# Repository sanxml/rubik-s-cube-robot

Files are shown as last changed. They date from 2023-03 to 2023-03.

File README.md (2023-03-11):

# 双臂魔方机器人

- [双臂魔方机器人](#双臂魔方机器人)
  - [设备总体设计方案](#设备总体设计方案)
    - [整体流程](#整体流程)
  - [硬件设计](#硬件设计)
    - [机械结构](#机械结构)
  - [软件设计](#软件设计)
    - [运动控制算法设计](#运动控制算法设计)
    - [图像处理设计](#图像处理设计)
    - [魔方算法设计](#魔方算法设计)
    - [GUI界面设计](#gui界面设计)

## 设备总体设计方案

### 整体流程

整体流程为:本作品以Arduino UNO单片机为控制核心，树莓派为图形处理核心。用DM542C数字驱动器驱动42步进电机实现机器手臂的“手腕”转动，单片机发送PWM信号能够控制20kg大扭矩数字伺服电机，以实现机器人手臂的“手指”收合。我们使用树莓派外接7寸显示屏和自主设计的GUI界面作为显示和操作终端，通过摄像头识别魔方颜色，通过树莓派对结果进行处理，用串口发送机器手臂的可执行信号给Arduino UNO，再通过Arduino控制机械手臂，完成魔方的复原。

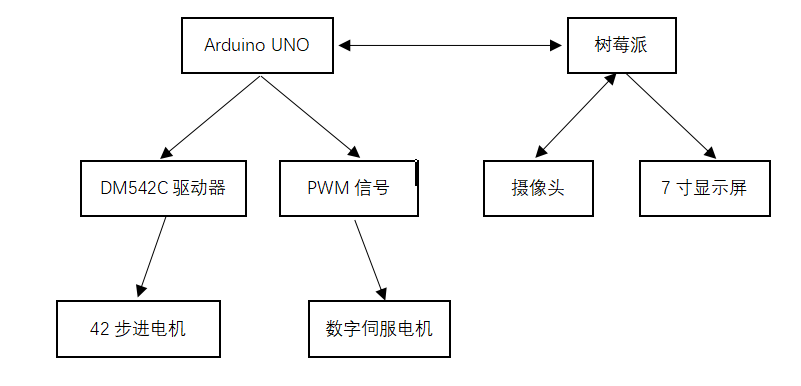
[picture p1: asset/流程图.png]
流程图


## 硬件设计

### 机械结构

本作品的总体机械结构呈现直立双臂魔方机器人，包括机械手臂和摄像头支架等。魔方采用斜放放置，摄像头俯视整个魔方，确保加快魔方的颜色识别。机械臂转动驱动使用步进电机，机械爪使用平行爪，确保平稳的抓取魔方，总体三维建模使用solidworks软件，三维模型文件在 model 目录下。

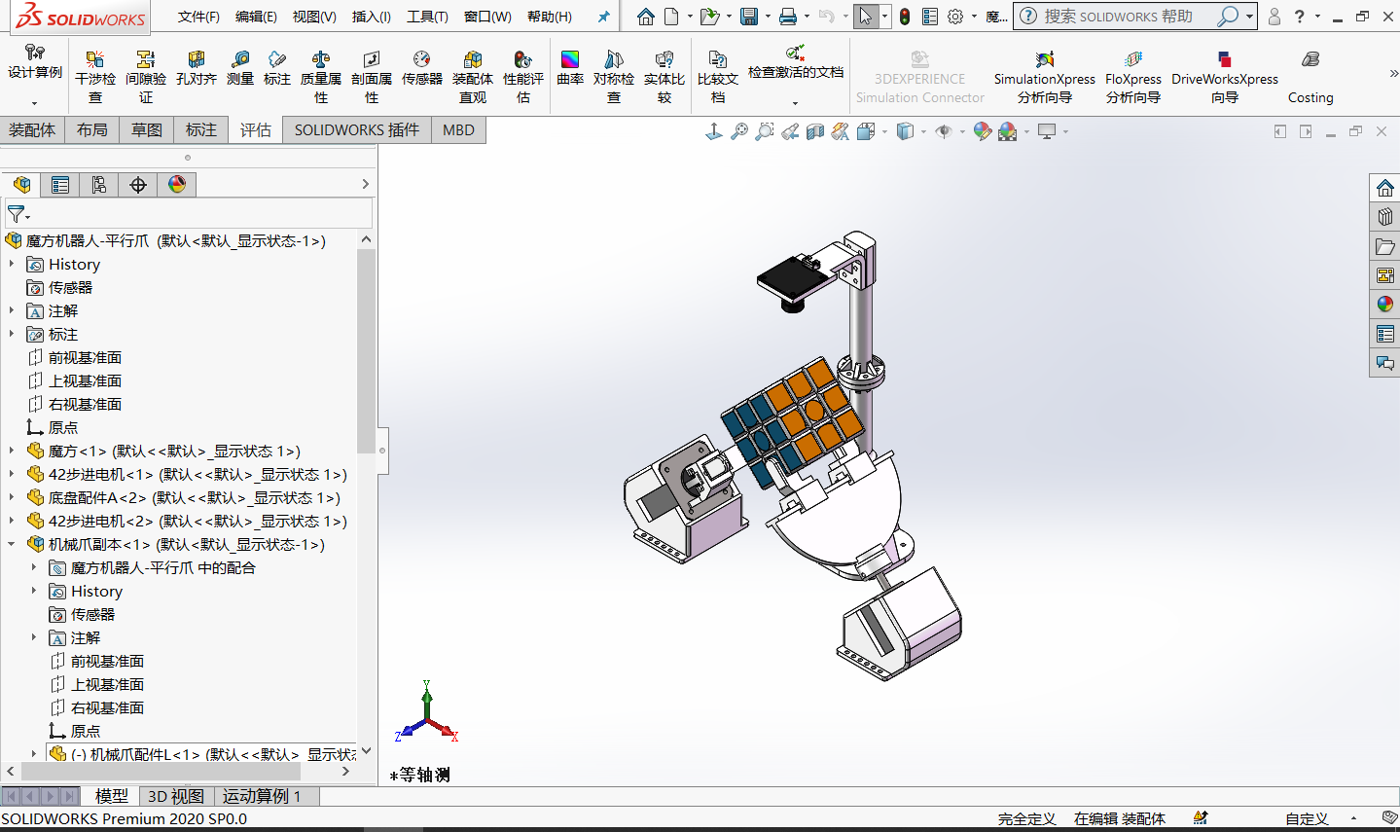
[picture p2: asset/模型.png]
模型


## 软件设计

### 运动控制算法设计

运动控制采用Arduino UNO单片机实现，使用串口连接树莓派，等待树莓派对魔方状态进行程序分析，得到魔方还原序列发送给Arduino UNO单片机。Arduino UNO单片机再将数据进行处理，控制电机实现魔方的复原。

步进电机属于开环系统，容易出现丢步和抖动等现象，硬件上对输入电流的控制和驱动器细分选择外，软件上还可以通过缓慢启停步进电机实现，通过改变给步进电机驱动器的脉冲快慢可以实现，具体实现代码如下

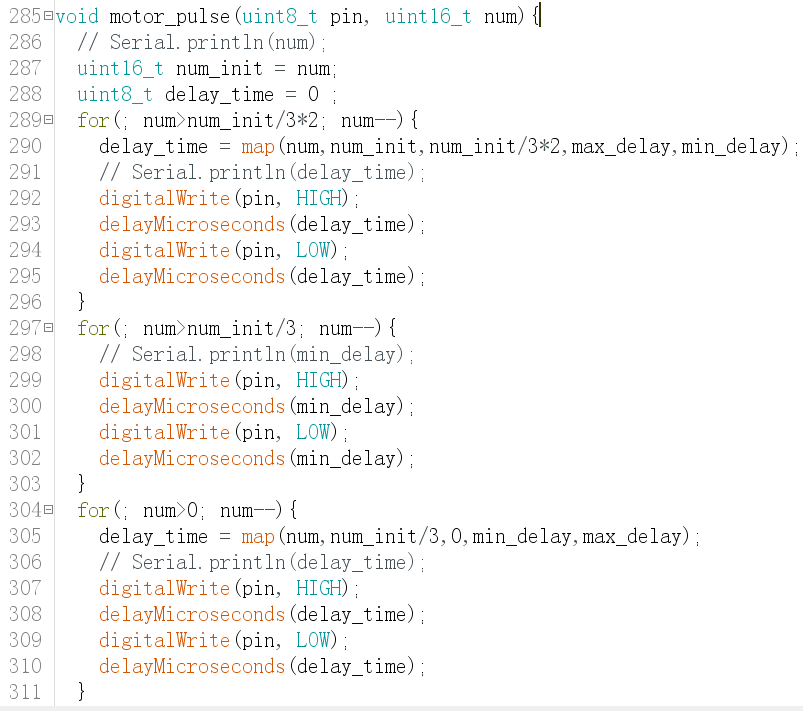
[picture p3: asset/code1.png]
code1


除此之外，步进电机如果一直往一个方向转动，会使舵机的信号线和机器手臂缠绕。为了避免这种情况发生，我们为每一个机器手臂设置一个标志变量，每次执行180度转动时，反转标志位，使下一次180度转动为相反反向。具体实现代码如下。

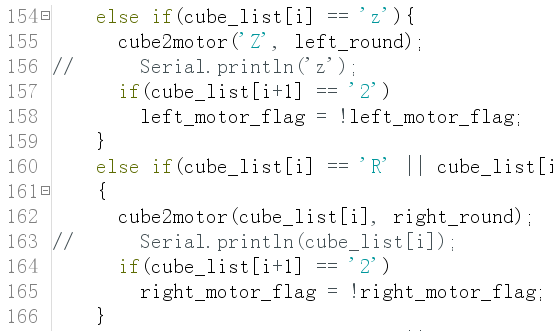
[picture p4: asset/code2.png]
code2


具体控制代码见[代码](code/arduino/cube12_01.ino)

### 图像处理设计

本作品中图像处理的整体思路：使用树莓派控制摄像头进行拍摄，把魔方的初始状态拍成图片，处理图片并将魔方每一面的颜色和魔方的位置存储到文本中；再对存储的文本内容进行分析，采用二阶段算法得到还原魔方的解法，再将六面转动解法通过优化生成二指还原解法，发送给Arduino UNO单片机对魔方进行复原。

图像处理程序均用python编程语言和opencv图像处理库实现。树莓派发送转动指令给Arduino单片机，转动三次，一次拍摄两面，将魔方初始状态通过照片存储起来。先对图片进行简单的高斯模糊去噪处理，再分割成单面图像。因为魔方位置是固定的，这里只需要对图片的特定位置进行分割，再通过文本矫正将不规则的梯形转成矩形，分割前后的图片和分割部分的关键程序代码分别如下图。

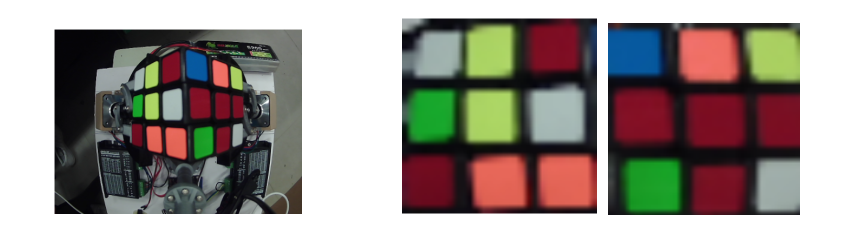
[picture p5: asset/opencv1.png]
opencv1


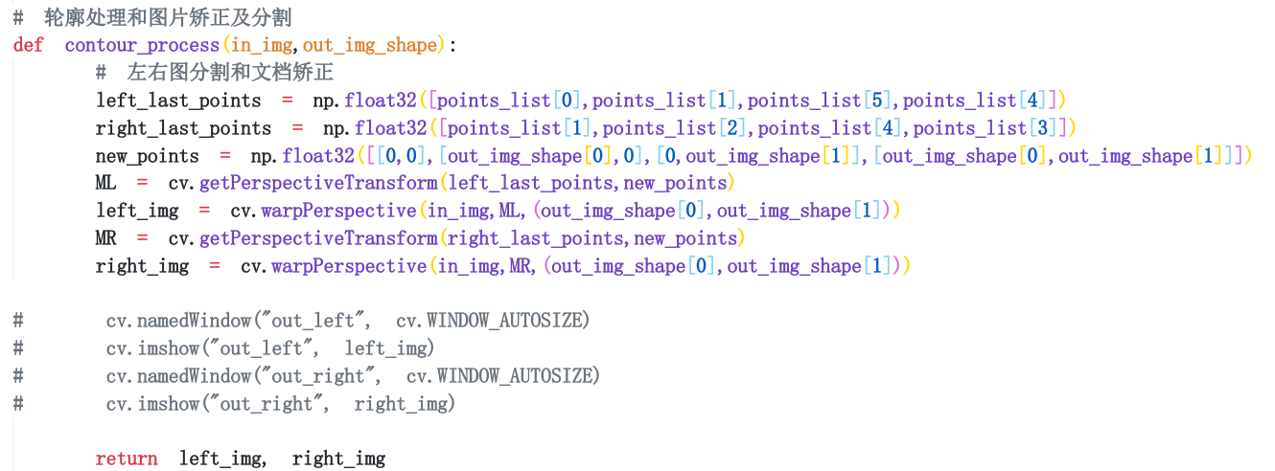
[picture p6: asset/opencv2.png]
opencv2


颜色识别采用将图片色彩空间从传统的RGB转换成HSV和LAB，HSV即色相(Hue)、饱和度(Saturation)、明度(Value)，又称HSB(B即Brightness)。H色相是色彩的基本属性，HSV色彩空间对颜色判断灵敏，且颜色识别时不易受明亮度的影响；Lab颜色被设计来接近人类视觉。它致力于感知均匀性，它的L分量密切匹配人类亮度感知。因此可以被用来通过修改a和b分量的输出色阶来做精确的颜色平衡，或使用L分量来调整亮度对比。

两种色彩空间都可以有效的减少因为环境光增加识别魔方的难度，这里采用双色彩空间进行矫正，RGB和LAB色彩空间、HSV色彩空间的对比图如下。

opencv3

在图片分割矫正和色彩空间转换后，就要将魔方每一个面的九个色块的LAB和HSV色彩空间的值都存储起来，以便后续进行颜色识别分类，相应代码如下图。

具体图像处理代码见[代码](code/raspberry-pi/cube.py)

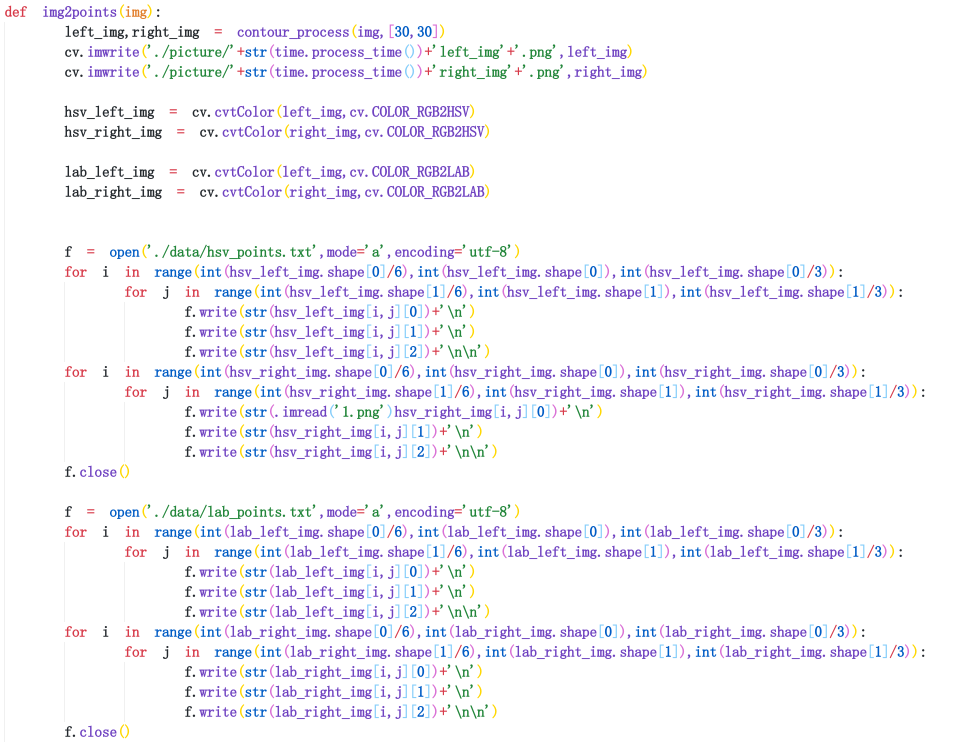
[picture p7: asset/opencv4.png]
opencv4


最后的就是程序最为重要的颜色识别分类，我采用的是多次循环HSV和LAB双色彩空间矫正的K-means聚类算法，对不同的光照的环境都能很好的识别。HSV和LAB色彩空间识别生成的三维图分别如下图。

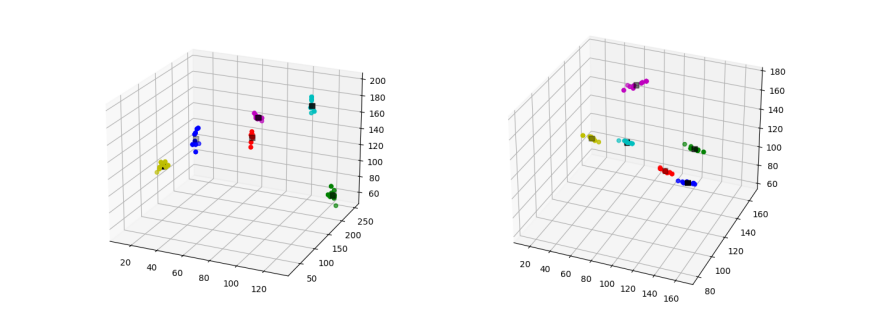
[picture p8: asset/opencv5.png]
opencv5


具体聚类代码见[代码](code/raspberry-pi/kmeans.py)

### 魔方算法设计

解魔方比赛中，主流的魔方解法，无论是从入门的层先，到进阶的CFOP、桥式，都是从部分到整体的思路，逐块还原魔方。这种方法之所以能在速拧比赛中广泛应用，依赖于人眼与人脑快速反应的结合，但这种解法并不适合与计算机。

机器的优势在于广度搜索与深度搜索能力，解魔方算法采用二阶段算法，也称为Kociemba算法，通过降低魔方的混乱程度，达到复原的效果。这种魔方解法的步数可以控制在21步以内，通过转换为二指解法也不过需要四十到七十步左右，二阶段算法还原魔方的示意图如图

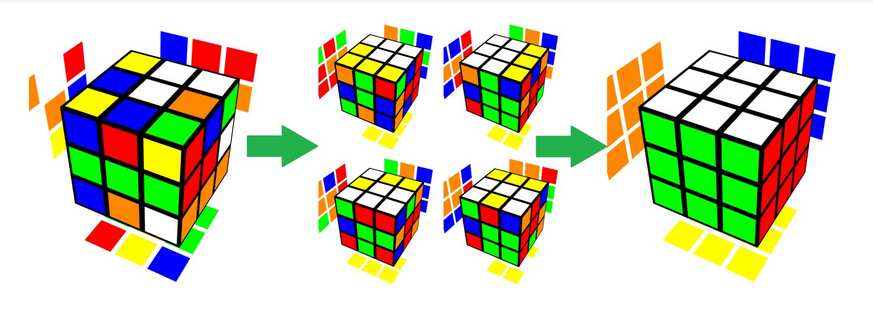
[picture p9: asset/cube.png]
cube


仅仅通过前面采集到的魔方每一面的颜色序列，还不能直接使用二阶段算法，需要提前设置每一面的相对位置，例如设定为白上绿前，但这是不现实的，不能得知乱魔方放置的初始位置，通过归类，可以得到一共由8种不同的相对位置。判断识别面中心的顺序，可以旋转面的颜色序列，达到实现白上绿前的相对位置。

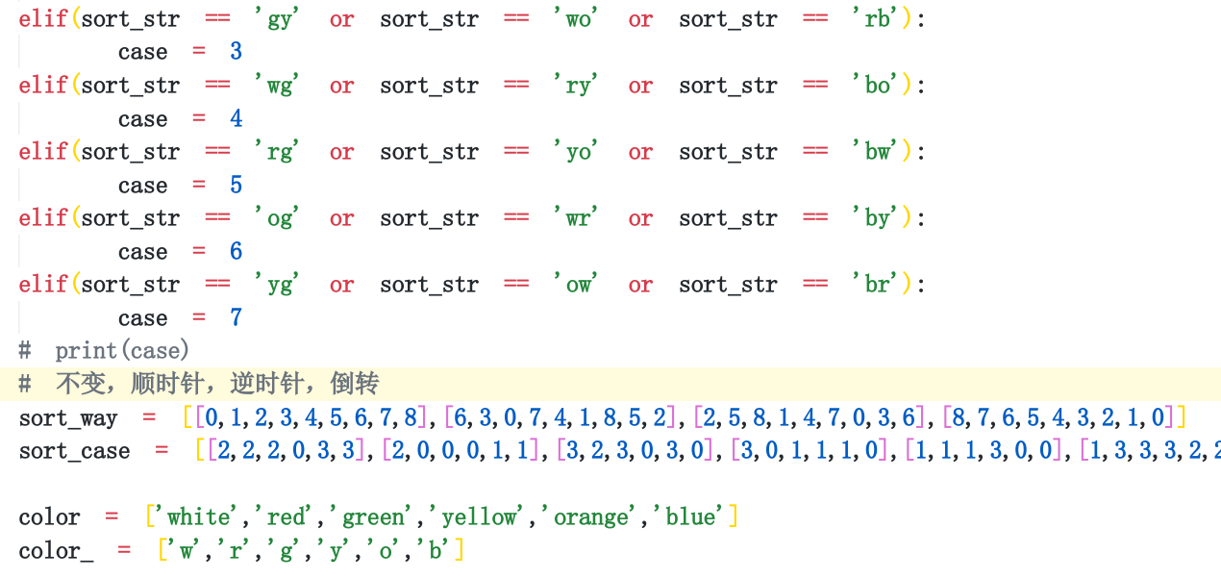
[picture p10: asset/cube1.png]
cube1


在调整旋转对应面的模仿序列后，还需要添加实际魔方序列和设定魔方序列 ”白上绿前”的相互关系，即将任意序列转到设定序列的转动步骤，则读取识别面的顺序文件，得到识别的前两面，即得到实际坐标。

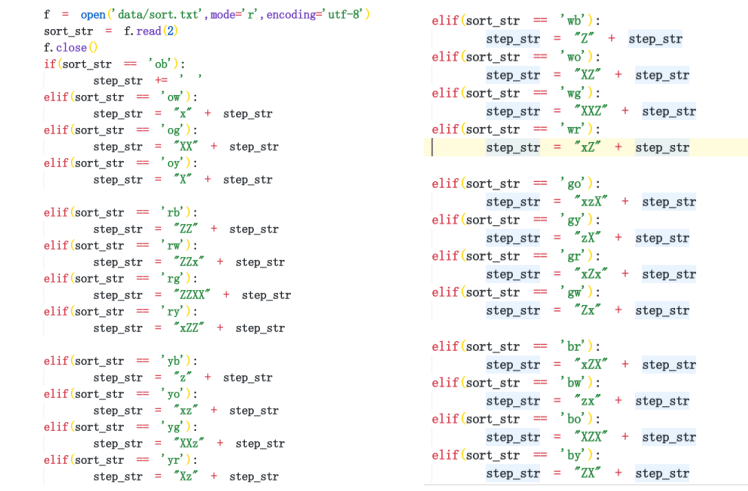
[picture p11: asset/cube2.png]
cube2


就可以使用二阶段算法了。使用二阶段算法，针对任意一个乱魔方都可以得到一串只有不到21步的还原公式。本作品设计的是一款双臂的魔方机器人，无法同时对六个面进行转动；通过对另外只能间接控制的面转换成两个可以同时控制的面的公式，即可实现通过双臂机器人还原魔方。转换后，得到的还原公式还比较繁琐，需要进一步优化，例如顺时针旋转一面三圈相当于逆时针旋转一圈。转换过程如图所示。

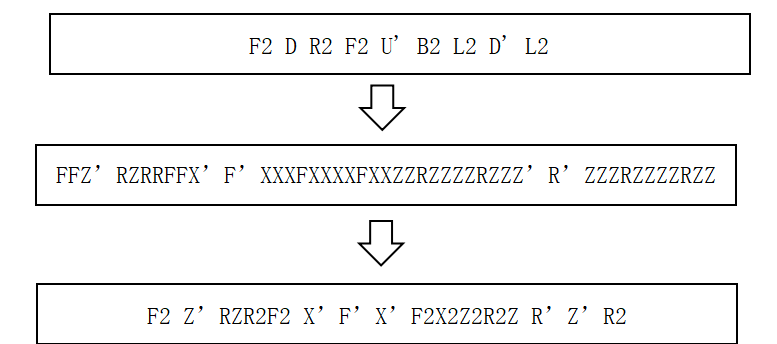
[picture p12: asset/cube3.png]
cube3


具体魔方算法代码见[代码](code/raspberry-pi/solution.py)

### GUI界面设计

本作品使用一块树莓派外接7寸显示屏，可触控。决定设计一个GUI交互界面，方便显示魔方的实况和解法等信息，以及可以实现一键解魔方的功能。

GUI界面主要由四部分组成，左上部分为摄像头的实时图像，可以方便显示魔方的实况；右上部分为识别到的魔方序列图解，可以全面的显示识别结果以及魔方整体的初始状态；左下部分为文本框，显示魔方的解法等信息；右下角有两个用户按键，一个可以发送转动信号，得到魔方的初始状态，另一个则是一键运行解魔方程序，具体界面如图5-3-1所示。

具体GUI界面代码见[代码](code/raspberry-pi/gui.py)

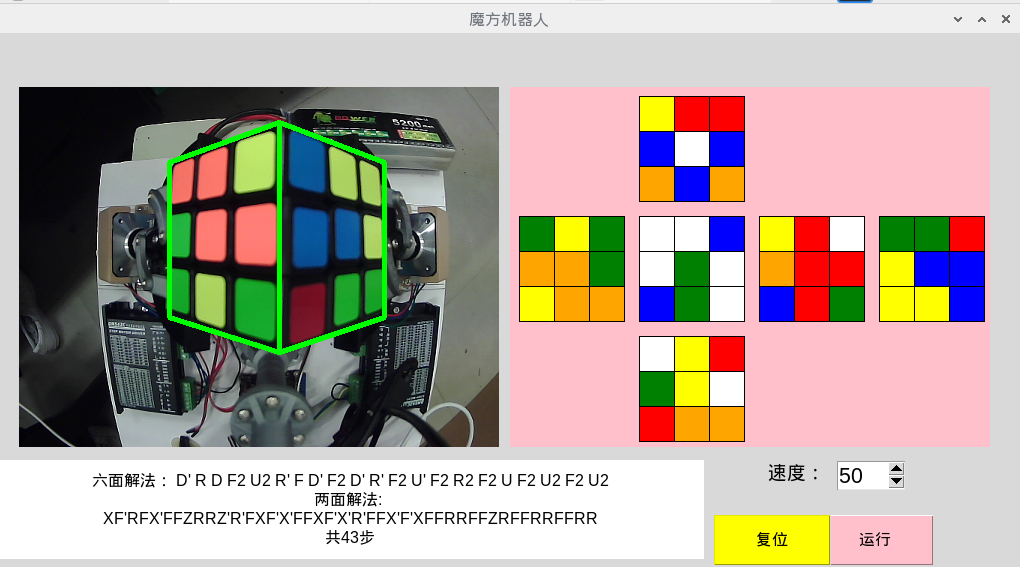
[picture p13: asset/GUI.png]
GUI


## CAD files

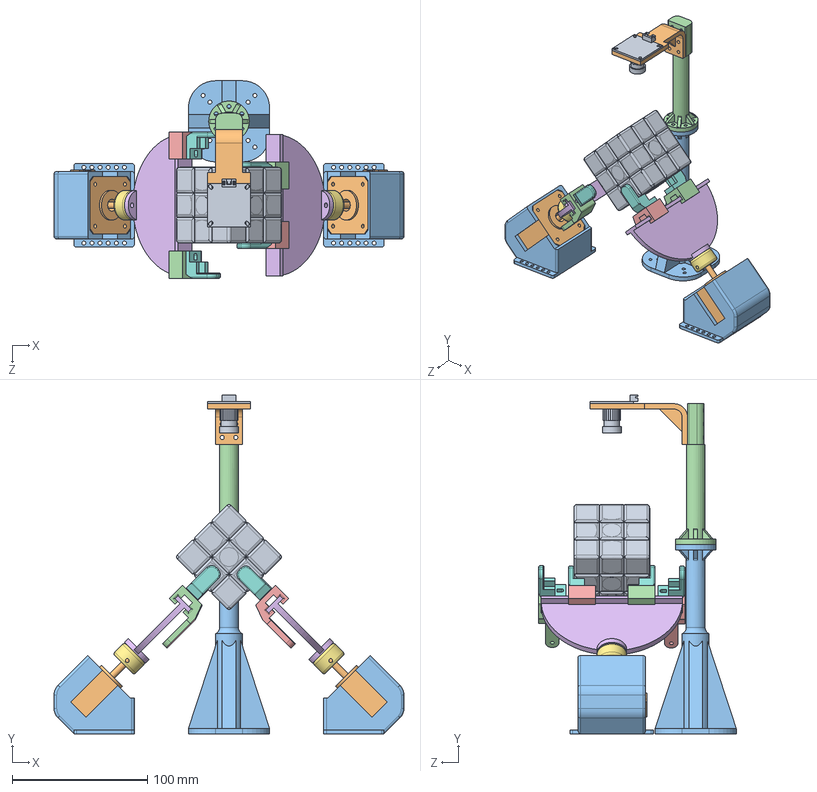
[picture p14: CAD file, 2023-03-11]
model/魔方机器人-平行爪.SLDASM
258.6 x 250.3 x 146.0 mm
魔方
42步进电机 x 2
底盘配件A x 2
机械爪配件L x 2
机械爪配件R x 2
机械爪配件A x 2
机械爪配件B x 2
机械爪配件C x 4
usb摄像头
底盘配件B
底盘配件C
底盘配件D

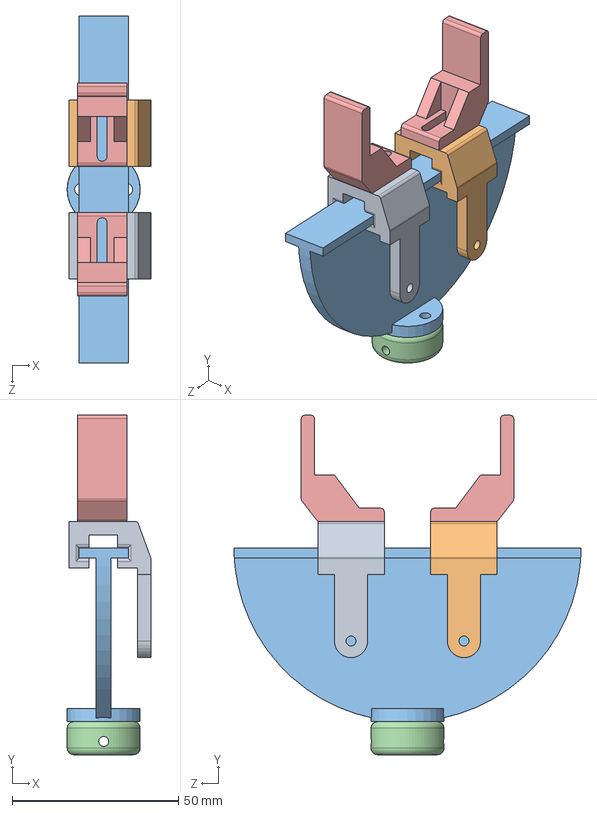
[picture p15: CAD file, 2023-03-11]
model/机械爪副本.SLDASM
25.2 x 102.2 x 104.5 mm
机械爪配件L
机械爪配件R
机械爪配件A
机械爪配件B
机械爪配件C x 2

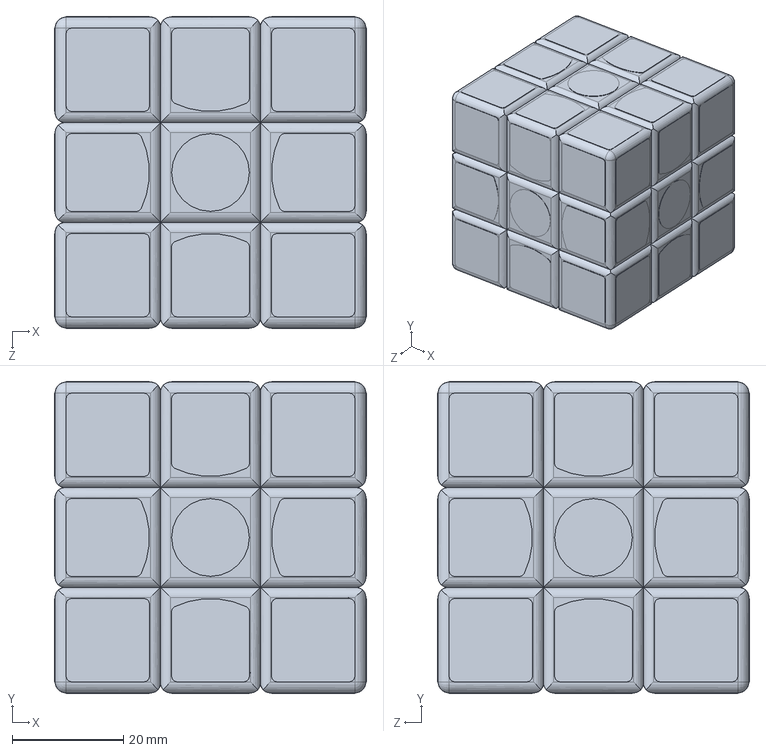
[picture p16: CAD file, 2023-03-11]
model/魔方.SLDPRT
56.2 x 56.2 x 56.2 mm

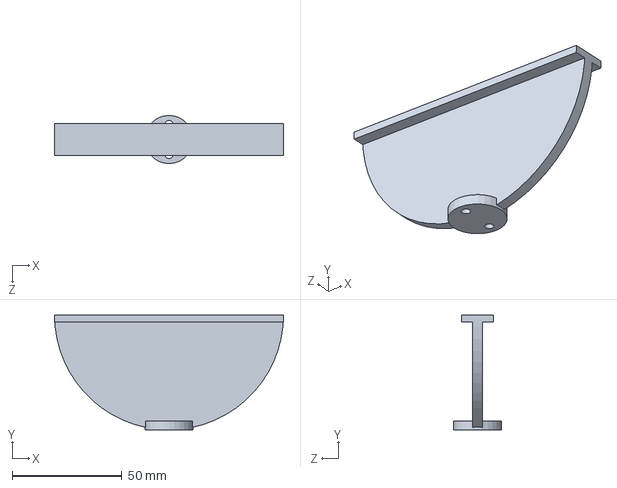
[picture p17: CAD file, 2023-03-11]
model/机械爪配件A.SLDPRT
104.5 x 52.2 x 22.0 mm

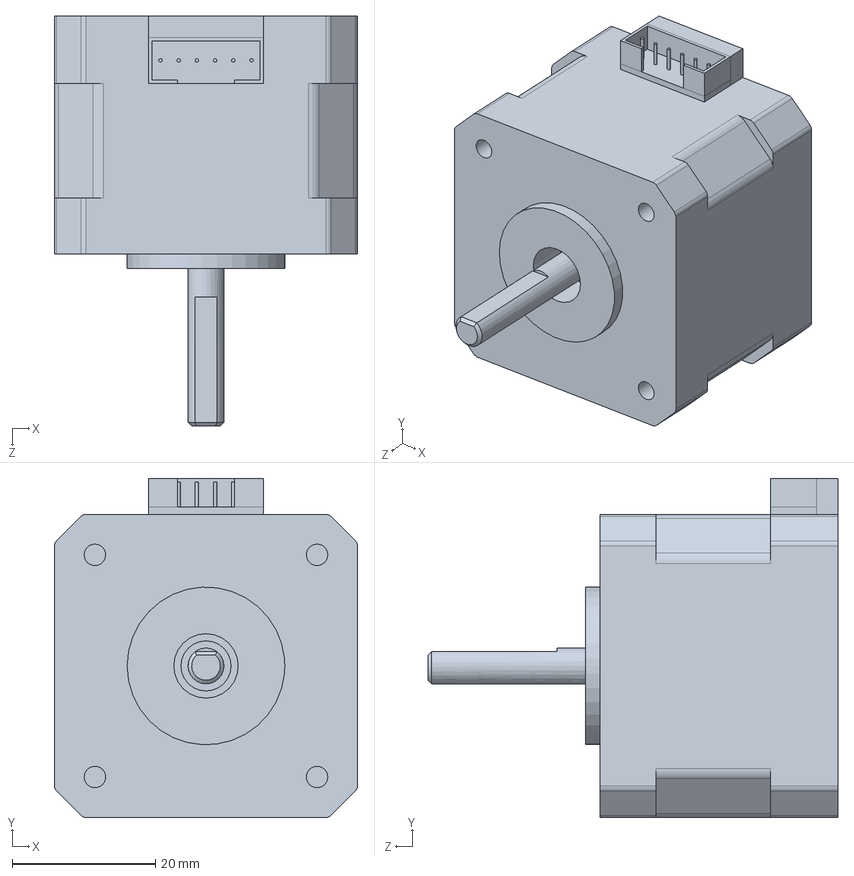
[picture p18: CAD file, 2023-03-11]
model/42步进电机.SLDPRT
42.3 x 47.3 x 57.2 mm

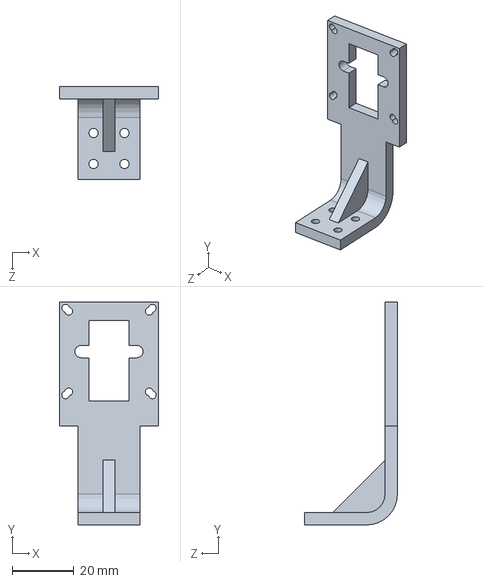
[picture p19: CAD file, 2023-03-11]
model/底盘配件B.SLDPRT
32.0 x 72.0 x 30.0 mm

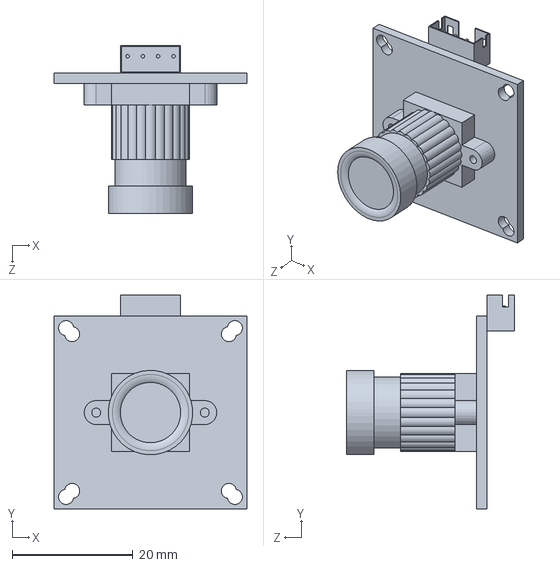
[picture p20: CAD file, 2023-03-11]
model/usb摄像头.SLDPRT
32.0 x 35.5 x 27.9 mm

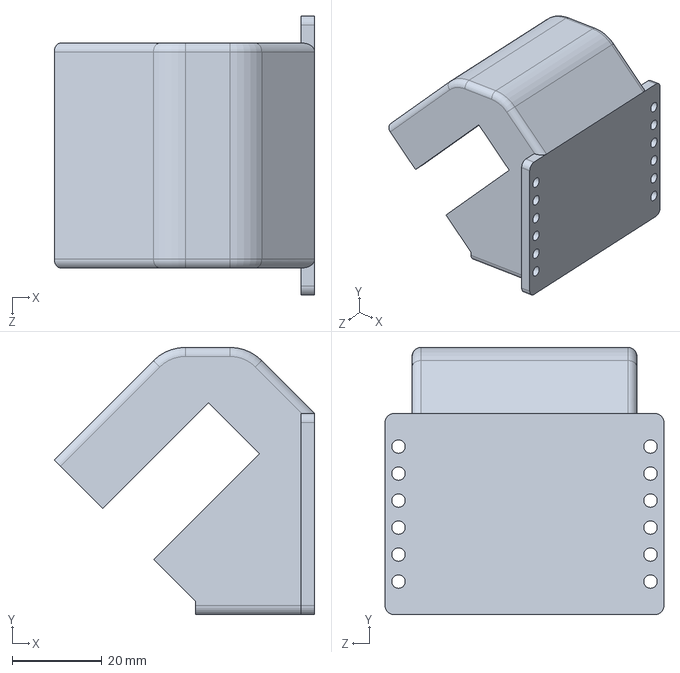
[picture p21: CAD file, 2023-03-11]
model/底盘配件A.SLDPRT
57.9 x 59.4 x 62.0 mm

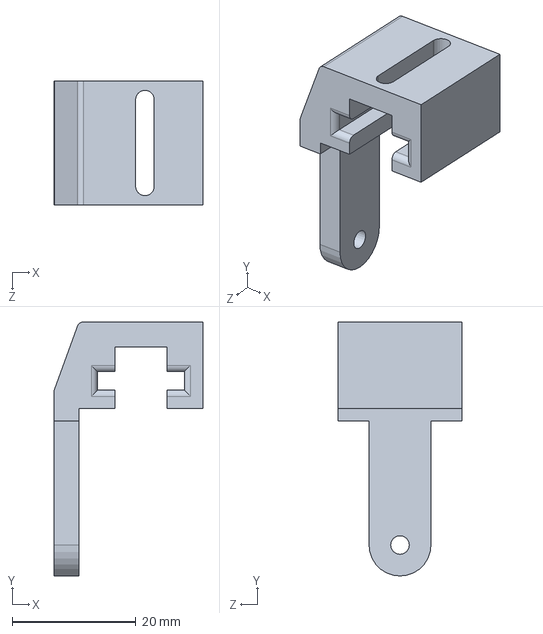
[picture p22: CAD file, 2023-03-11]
model/机械爪配件L.SLDPRT
24.0 x 41.0 x 20.0 mm

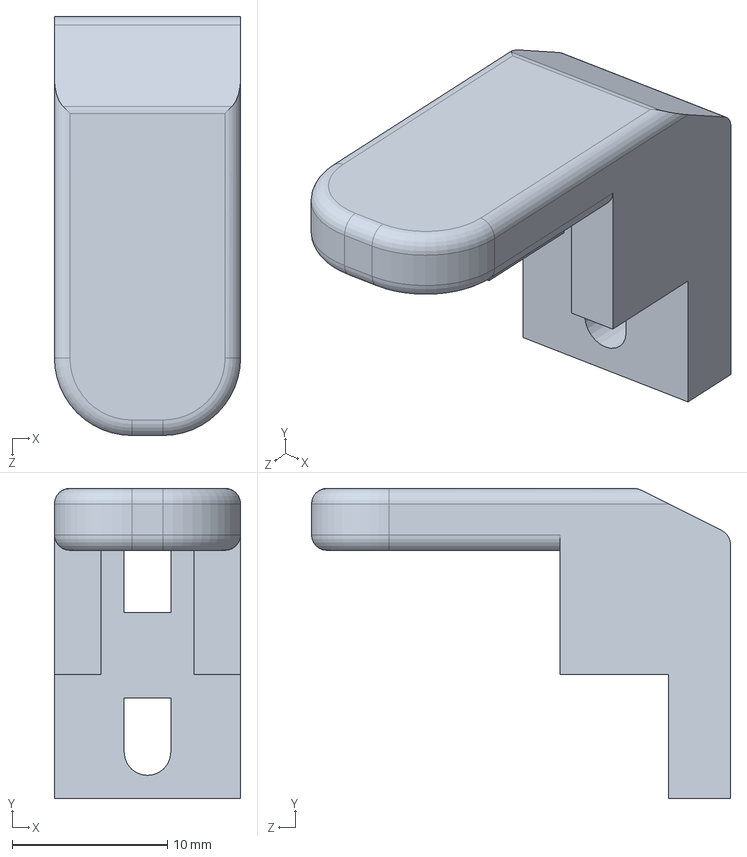
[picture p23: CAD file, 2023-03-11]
model/机械爪配件C.SLDPRT
12.0 x 20.0 x 27.0 mm

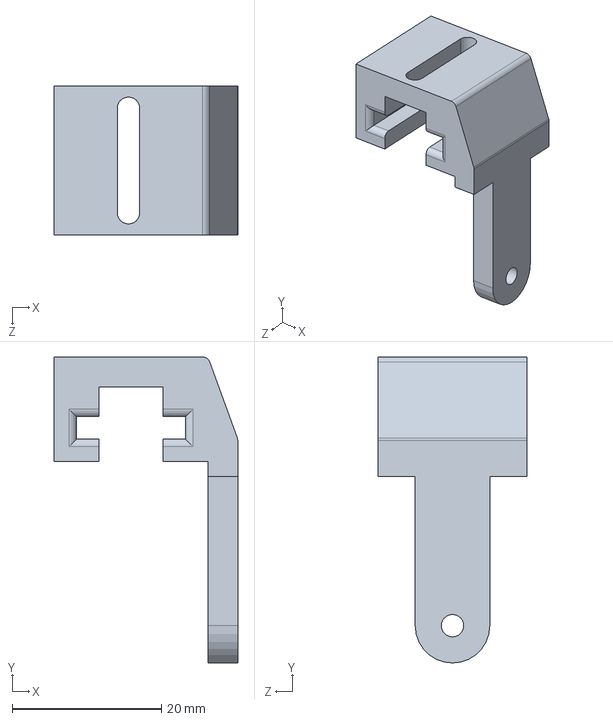
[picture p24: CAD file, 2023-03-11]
model/机械爪配件R.SLDPRT
24.6 x 41.0 x 20.0 mm

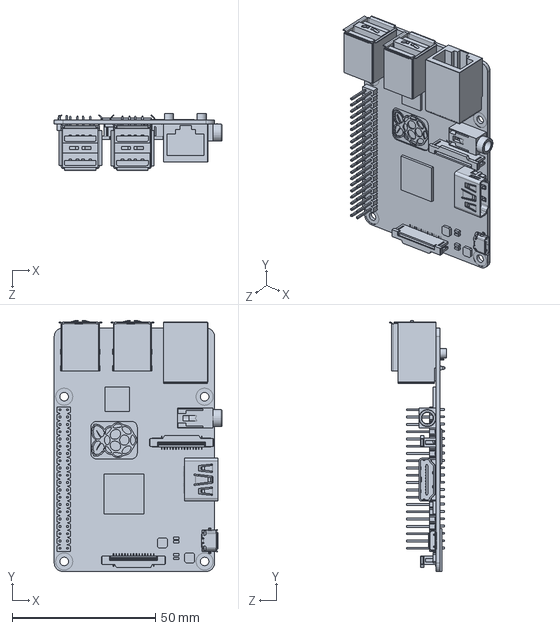
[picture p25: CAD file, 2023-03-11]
model/树莓派3b.SLDPRT
58.5 x 87.6 x 19.8 mm

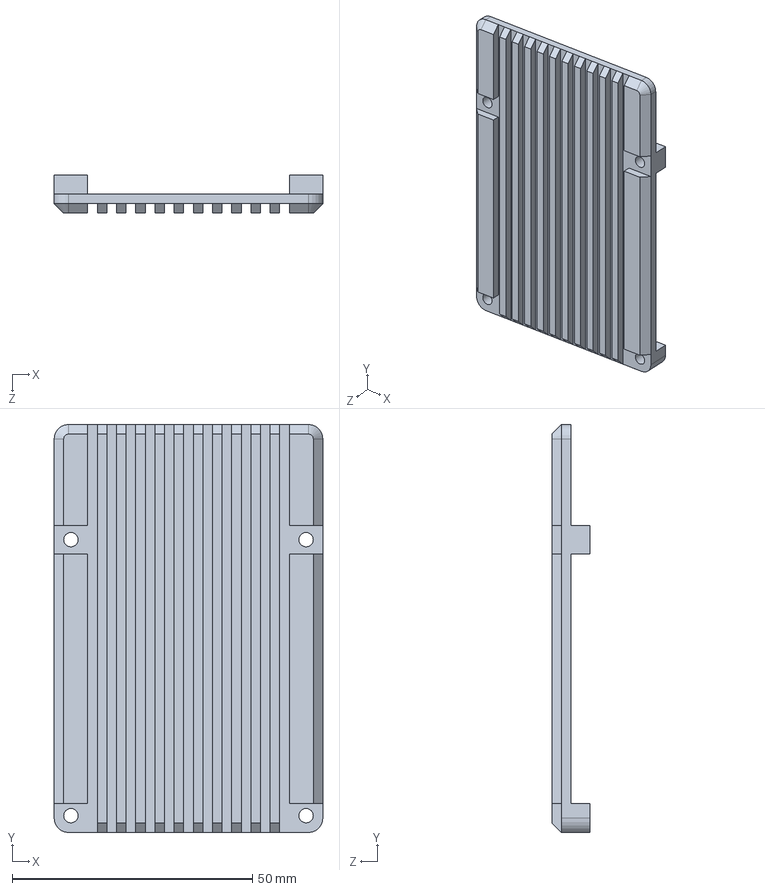
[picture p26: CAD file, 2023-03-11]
model/树莓派底壳.SLDPRT
56.0 x 85.0 x 8.00 mm

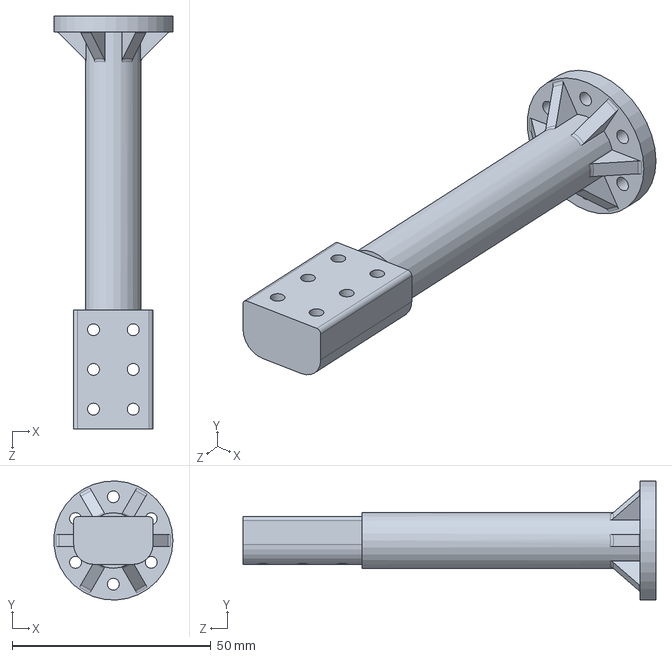
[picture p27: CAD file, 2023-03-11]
model/底盘配件D.SLDPRT
29.9 x 30.0 x 104.0 mm

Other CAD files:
model/机械爪.SLDASM
model/树莓派CSI摄像头.SLDPRT
model/机械爪配件B.SLDPRT
model/底盘配件C.SLDPRT

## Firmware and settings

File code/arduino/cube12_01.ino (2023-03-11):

#include <Servo.h>

#define MOTOR1_CP 3
#define MOTOR1_DIR 4
#define MOTOR1_EN 5
#define MOTOR2_CP 6
#define MOTOR2_DIR 7
#define MOTOR2_EN 8
#define SERVO1 10
#define SERVO2 11

#define MOTOR_PULSE 6400 //转一圈的脉冲

Servo servo_left, servo_right;
uint8_t servo_left_state[4] = {24,38,88,44};// 闭合 紧贴 张开
uint8_t servo_right_state[4] = {24,38,88,44};// 闭合 紧贴 张开  

uint8_t min_delay = 54 , max_delay = 800;

void setup()
{
//  pinMode(LED_BUILTIN, OUTPUT);
  pinMode(MOTOR1_CP, OUTPUT);
  pinMode(MOTOR1_DIR, OUTPUT);
  pinMode(MOTOR1_EN, OUTPUT);
  pinMode(MOTOR2_CP, OUTPUT);

  pinMode(MOTOR2_DIR, OUTPUT);
  pinMode(MOTOR2_EN, OUTPUT);
  digitalWrite(MOTOR1_DIR, HIGH);
  digitalWrite(MOTOR1_EN, LOW);
  digitalWrite(MOTOR2_DIR, HIGH);
  digitalWrite(MOTOR2_EN, LOW);

  Serial.begin(115200); //打开串口

  servo_left.attach(SERVO1,500,2500);
  servo_right.attach(SERVO2,500,2500);

  servo_left.write(servo_left_state[3]);
  servo_right.write(servo_right_state[3]);
  delay(200);

//  servo_left.write(servo_left_state[0]);
//  delay(500);
//  servo_right.write(servo_right_state[2]);
//  delay(3000);
//  servo_left.write(servo_left_state[3]);
//  servo_right.write(servo_right_state[3]);
//  delay(3000);
//  servo_left.write(servo_left_state[2]);
//  servo_right.write(servo_right_state[0]);
//  delay(3000);
}

void loop(){

  String buf = "";
  while (Serial.available() == 0);
  while (Serial.available() > 0){
      buf += char(Serial.read());
      delay(5);
  }
  
  if(buf.length()>=65){
    Serial.flush();
    while (Serial.available() == 0);
    while (Serial.available() > 0){
      buf += char(Serial.read());
      delay(5);
    }
  }
  //Serial.print(buf.length());
  motor_solution(buf);
  Serial.println(buf);
  Serial.flush();

} 

//L2 D2 R' F2 D2 F2 U2 L' B2 D2 L' F' D' L U2 R D F' U L
//rzrzRRzRzFZZrZZxfxFXXrZRzRzrZFFzRZRRFFxfxFFXXZZRRZrzRR
//R' D' L2 U F L' U' B R' U R D' F2 D R2 F2 U' B2 L2 D' L2
//L2 D L2 B2 U F2 R2 D' F2 D R' U' R B' U L F' U' L2 D R

void motor_solution(String cube_list){
  uint8_t i = 0;
  for(; i<cube_list.length(); i++){
    // Serial.print(cube_list[i]);
    if(cube_list[i] == 'S'){
      uint8_t cube_speed = (uint8_t)cube_list[i+1]*10 + (uint8_t)cube_list[i+2] - 16;
      Serial.print("Speed = ");
      Serial.println(cube_speed);
      min_delay = cube_speed;
      cube_list = ' ';
   }
    char temp = cube_list[i];
    if (temp == cube_list[i+1]){
      cube_list[i+1] = '2';
      i++;
    }
  }
  // Serial.println(cube_list);
  uint8_t left_motor_flag = 0, right_motor_flag = 0;
  for(i=0; i<cube_list.length(); i++){
    int8_t left_round, right_round;
    if(cube_list[i] == 'r' || cube_list[i] == 'f' || cube_list[i] == 'x' || cube_list[i] == 'z')
      left_round = right_round = -1;
    else
      left_round = right_round = 1;

    if(cube_list[i+1] == '2'){
      if(left_motor_flag == 0)
        left_round = 2;
      else
        left_round = -2;
      if(right_motor_flag == 0)
        right_round = 2;
      else
        right_round = -2;
    }
    if(cube_list[i] == 'r'){
      cube2motor('R', right_round);
//      Serial.println('r');
      if(cube_list[i+1] == '2')
        right_motor_flag = !right_motor_flag;
    }
    else if(cube_list[i] == 'f'){
      cube2motor('F', left_round);
//      Serial.println('f');
      if(cube_list[i+1] == '2')
        left_motor_flag = !left_motor_flag;
    }
    else if(cube_list[i] == 'x'){
      cube2motor('X', right_round);
//      Serial.println('x');
      if(cube_list[i+1] == '2')
        right_motor_flag = !right_motor_flag;
    }
    else if(cube_list[i] == 'z'){
      cube2motor('Z', left_round);
//      Serial.println('z');
      if(cube_list[i+1] == '2')
        left_motor_flag = !left_motor_flag;
    }
    else if(cube_list[i] == 'R' || cube_list[i] == 'X')
    {
      cube2motor(cube_list[i], right_round);
//      Serial.println(cube_list[i]);
      if(cube_list[i+1] == '2')
        right_motor_flag = !right_motor_flag;
    }
    else if(cube_list[i] == 'F' || cube_list[i] == 'Z')
    {
      cube2motor(cube_list[i], left_round);
//      Serial.println(cube_list[i]);
      if(cube_list[i+1] == '2')
        left_motor_flag = !left_motor_flag;
    }
    else if(cube_list[i] == 'C'){
      cube2motor('C', right_round);
//      Serial.println('C');
    }
    else if(cube_list[i] == 'c'){
      servo_left.write(servo_left_state[3]);
      servo_right.write(servo_right_state[3]);
//      Serial.println('c');
    }
    else if(cube_list[i] == 'l'){
      servo_left.write(servo_left_state[0]);
      servo_right.write(servo_right_state[0]);
//      Serial.println('l');
    }
    if(cube_list[i+1] == '2'){
      i++;
//      Serial.println('2');
    }
  }
}

void cube2motor(char cube_list, int8_t round){
  servo_left.write(servo_left_state[0]);
  servo_right.write(servo_right_state[0]);
  delay(80);
  if(cube_list == 'R'){
    servo_right.write(servo_right_state[1]);
    motor_turning('R', round);
    if(round == 1 || round == -1){
      servo_right.write(servo_right_state[2]);
      delay(100);
      motor_turning('R', -round);
    }
  }
  else if(cube_list == 'F'){
    servo_left.write(servo_left_state[1]);
    motor_turning('L', round);
    if(round == 1 || round == -1){
      servo_left.write(servo_left_state[2]);
      delay(100);
      motor_turning('L', -round);
    }
  }
  else if(cube_list == 'X'){

    if(round == 1 || round == -1){
      servo_right.write(servo_right_state[2]);
      delay(100);
      motor_turning('R', -round);
      servo_right.write(servo_right_state[0]);
      delay(80);
      servo_left.write(servo_left_state[2]);
      delay(100);
      motor_turning('R', round);
    }
    else{
      servo_left.write(servo_left_state[2]);
      delay(100);
      motor_turning('R', round);
      servo_left.write(servo_left_state[3]);
      delay(80);
      servo_right.write(servo_right_state[3]);
      delay(100);
    }

  }
  else if(cube_list == 'Z'){
    if(round == 1 || round == -1){
      servo_left.write(servo_left_state[2]);
      delay(100);
      motor_turning('L', -round);
      servo_left.write(servo_left_state[0]);
      delay(80);
      servo_right.write(servo_right_state[2]);
      delay(100);
      motor_turning('L', round);
    }
    else{
      servo_right.write(servo_right_state[2]);
      delay(100);
      motor_turning('L', round);
      servo_right.write(servo_right_state[3]);
      delay(80);
      servo_left.write(servo_left_state[3]);
      delay(100);
    }
  }
  if(cube_list == 'C'){
      servo_right.write(servo_right_state[3]);
      servo_left.write(servo_left_state[3]);
      delay(200);
      servo_right.write(servo_right_state[0]);
      servo_left.write(servo_left_state[0]);
  }
    
    servo_right.write(servo_right_state[0]);
    servo_left.write(servo_left_state[0]);
    delay(120);
    servo_right.write(servo_right_state[1]);
    servo_left.write(servo_left_state[1]);
    delay(50);
}

void motor_turning(char motor, float right_angle){
  uint8_t cp_pin = 0 , dir_pin = 0;
  if(motor == 'L'){
    cp_pin = MOTOR1_CP;
    dir_pin = MOTOR1_DIR;
  }
  else if(motor == 'R'){
    cp_pin = MOTOR2_CP;
    dir_pin = MOTOR2_DIR;
  }
  if(right_angle >= 0){
    digitalWrite(dir_pin, HIGH);
    motor_pulse(cp_pin, (int)(right_angle*MOTOR_PULSE/4));
    // Serial.println(right_angle*MOTOR_PULSE/4);
  }
  else if(right_angle < 0){
    digitalWrite(dir_pin, LOW);
    motor_pulse(cp_pin, -(int)(right_angle*MOTOR_PULSE/4));
  }
}

void motor_pulse(uint8_t pin, uint16_t num){
  // Serial.println(num);
  uint16_t num_init = num;
  uint8_t delay_time = 0 ;
//  for(; num>num_init/3*2; num--){
//    delay_time = map(num,num_init,num_init/3*2,max_delay,min_delay);
//    // Serial.println(delay_time);
//    digitalWrite(pin, HIGH);
//    delayMicroseconds(delay_time);
//    digitalWrite(pin, LOW);
//    delayMicroseconds(delay_time);
//  }
//  for(; num>num_init/3; num--){
//    // Serial.println(min_delay);
//    digitalWrite(pin, HIGH);
//    delayMicroseconds(min_delay);
//    digitalWrite(pin, LOW);
//    delayMicroseconds(min_delay);
//  }
//  for(; num>0; num--){
//    delay_time = map(num,num_init/3,0,min_delay,max_delay);
//    // Serial.println(delay_time);
//    digitalWrite(pin, HIGH);
//    delayMicroseconds(delay_time);
//    digitalWrite(pin, LOW);
//    delayMicroseconds(delay_time);
//  }

  for(; num>0; num--){
    digitalWrite(pin, HIGH);
    delayMicroseconds(min_delay);
    digitalWrite(pin, LOW);
    delayMicroseconds(min_delay);
  }
}

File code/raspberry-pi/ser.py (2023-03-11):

import serial
import time

#def main():
#    while True:
#        # 获得接收缓冲区字符
#        count = ser.inWaiting()
#        if count != 0:
#            # 读取内容并显示
#            recv = ser.read(count)
#            print(recv)
#        # 清空接收缓冲区
#        ser.flushInput()
#        # 必要的软件延时
#        time.sleep(0.1)
#
#if __name__ == '__main__':
#    try:
#    # 打开串口
#        ser = serial.Serial('/dev/ttyAMA0', 115200)
#        if ser.isOpen == False:
#            ser.open()                # 打开串口
#        ser.write(b"rRZzXfxFRRXX")
#        #ser.write(b"rzrzRRzRzFZZrZZxfxFXXrZRzRzrZFFzRZRRFFxfxFFXXZZRRZrzRR")
#        main()
#    except KeyboardInterrupt:
#        if ser != None:
#            ser.close()
arduino_ser = serial.Serial('/dev/ttyAMA0', 115200)

def ser_init():
    if arduino_ser.isOpen == False:
        arduino_ser.open()                # 打开串口

def ser_close():
    if arduino_ser != None:
        arduino_ser.close()

def ser_send(string):
    arduino_ser.write(string)


def ser_recv():
    while True:
        # 获得接收缓冲区字符
        count = arduino_ser.inWaiting()
        # 读取内容并显示
        if count == 0:
            break
        recv = arduino_ser.read(count)
        print(recv)
        # 清空接收缓冲区
        arduino_ser.flushInput()
        # 必要的软件延时
        time.sleep(0.1)
        return recv

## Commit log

2023-03-11 添加树莓派代码
2023-03-11 修改readme文件
